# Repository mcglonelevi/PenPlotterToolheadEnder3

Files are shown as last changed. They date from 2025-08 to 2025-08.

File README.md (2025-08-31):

# Pen Plotter for Ender 3 / Ender 3 V2
## Introduction
I had an old Ender 3 V2 that was sitting around collecting dust.  I thought it would be fun to make a pen plotter attachment for the Ender 3 V2.  In case others were interested in making it, I am making this open-source under the MIT license.

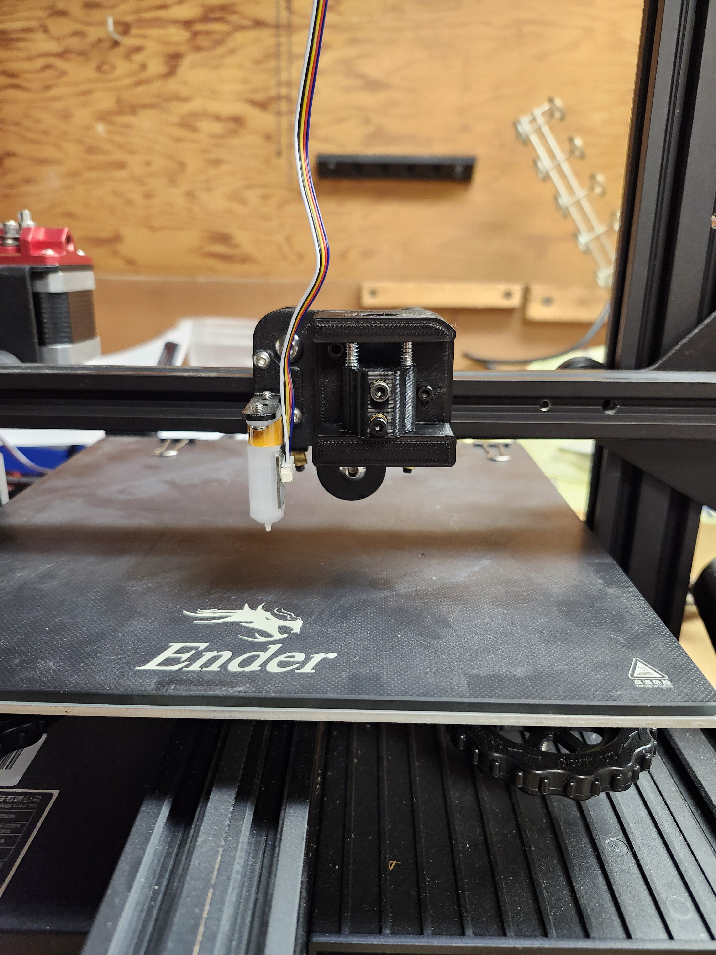
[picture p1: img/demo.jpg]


## Demo
I made a YouTube video showcasing the toolhead in action: https://www.youtube.com/watch?v=6iu8gkPlm34

## Design Constraints
I looked at other pen plotting attachments for the ender 3 V2.  I wanted the following features in my build:
1. I wanted the pen to have some pressure via springs to account for an unlevel bed.
2. I am running [Jyers Marlin firmware](https://github.com/Jyers/Marlin) on my Ender 3 V2 with a BL Touch.  I didn't want to install the old endstops, so I made my solution compatible with models of the Ender 3 with a BL touch.

## Bill of Materials
1. About 25 grams of PLA or equivalent of your preferred filament.
2. 3mm * 40mm steel rods (2).  I bought [these](https://www.amazon.com/Lyrlidr-Stainless-Industry-Working-Hobbies/dp/B0DCBCRB1C) on Amazon and cut them down to size.
3. 2 M3 brass inserts - I used [these](amazon.com/dp/B0CDH36ZMX?ref=ppx_yo2ov_dt_b_fed_asin_title)
4. 4 M3 screws.  I think M3x20mm should work for most cases.
5. 1 M3 nut.
6. 2 springs.  I used 0.3mm x 4mm x 15mm - Something [like these](https://www.amazon.com/PATIKIL-Compression-Stainless-Mechanical-Assortment/dp/B0DKCRH26S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,industrial,87&sr=1-1&th=1) should work.

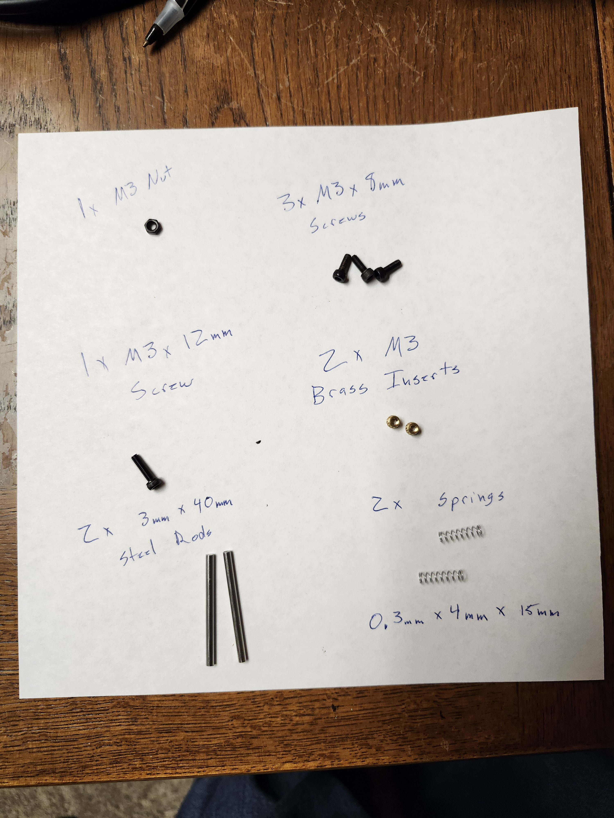
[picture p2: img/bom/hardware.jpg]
Hardware

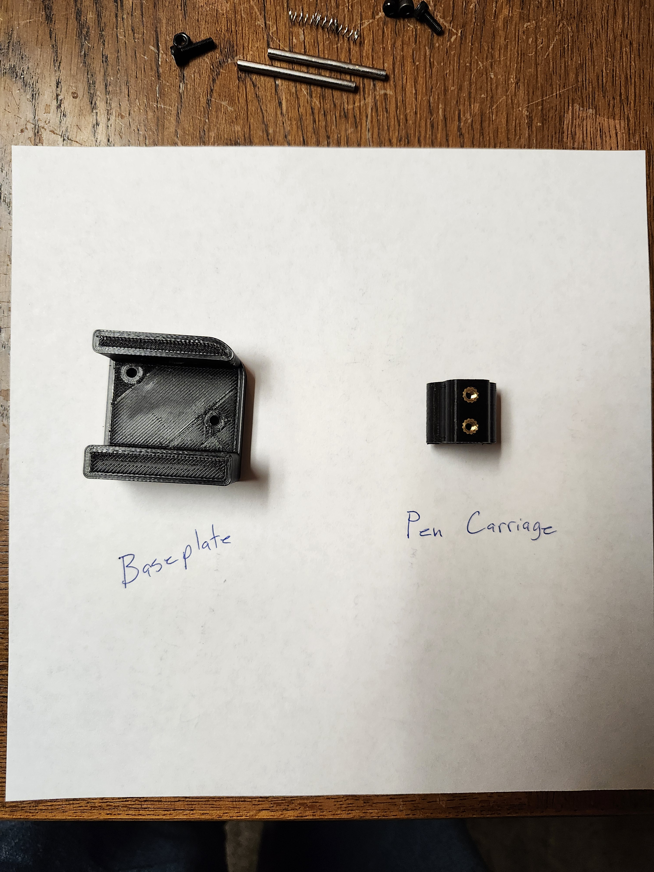
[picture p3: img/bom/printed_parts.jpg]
Printed Parts


## Recommended Print Settings
There are two parts to print in this build - the pen carriage and the base plate that attaches to the printer.  I printed both parts with 4 walls and 40% infill.  No support should be necessary, but there are a few overhangs.  The size of the overhangs are very small though.

## Quick Assembly Instructions
These instructions assume the toolhead and hotend have been removed from your Ender 3.  The instructions for this vary by model, but should involve unscrewing a screw in the back of the toolhead and then 2 screws for the hotend.

### Instructions
1. In the carriage, press 2 brass inserts into the front 2 screw holes.  Use a soldering iron to melt the plastic and press them into place.  For PLA, I would recommend a soldering temp ~525F or 200C [image](https://github.com/mcglonelevi/PenPlotterToolheadEnder3/blob/main/img/assembly/step_1.jpg)
2. Check the fit of the 3mm steel rods in the pen carriage.  The pen carriage should slide but not move.  Depending on the tolerances of your printer, you may need to use a 1/8in drill bit to expand the holes.  Also, some PTFE lube may also help things slide a little easier.
3. Insert the steel rods into the baseplate but do not push them all the way down. [image](https://github.com/mcglonelevi/PenPlotterToolheadEnder3/blob/main/img/assembly/step_3.jpg)
4. Slide the springs over the steel rods. [image](https://github.com/mcglonelevi/PenPlotterToolheadEnder3/blob/main/img/assembly/step_4a.jpg)
5. Compress the spring and move one side of the pen carriage into place and push the steel rod as far in as you can. [image](https://github.com/mcglonelevi/PenPlotterToolheadEnder3/blob/main/img/assembly/step_5a.jpg)  Compress the other spring and insert the other rod through the other hole in the pen carriage. [image](https://github.com/mcglonelevi/PenPlotterToolheadEnder3/blob/main/img/assembly/step_5b.jpg)
6: If the rods are not flush with the top, I would recommend a clamp or a vice or gently hammering the rod into place until its flush with the top.  It should be flush or close to flush with the top of the base plate if the length is close to 40mm. [image](https://github.com/mcglonelevi/PenPlotterToolheadEnder3/blob/main/img/assembly/step_6.jpg)
7. Using 2 M3 x 8MM screws, thread them into the brass inserts on the front of the pen carriage. [image](https://github.com/mcglonelevi/PenPlotterToolheadEnder3/blob/main/img/assembly/step_7.jpg)
8. The base plate has 2 holes for attaching the plate to the printer.  For the right hole, use an M3x8mm screw.  For the right hole, stick a M3x12mm screw through it and the screw should poke through the back of the plate.  Secure it with a nut. [image](https://github.com/mcglonelevi/PenPlotterToolheadEnder3/blob/main/img/assembly/step_8.jpg)

## Calibration
Here are my recommended calibration steps.
1. Using the prepare menu, home all the axes on your printer.  At the end of calibration, it's pretty likely that your Z height will be ~13mm.
2. Using the Move controls on the printer, set the Z axis to ~0.5mm.
3. Insert a pen and let it touch the build plate.  Turn both screws in the pen carriage to secure the pen in place.
4. Lift up on the pen slightly and put a piece of paper in place.  I secure the paper to the build plate with binder clips.
5. Using the controls on the printer, you can manually move the head around for a quick test.  Another option is to disable the stepper motors and move the gantry and bed by hand.  Assuming the lines look nice and solid, your printer is calibrated.

If your pen doesn't make contact with the paper, rerun the calibration steps above but use a slightly higher number on the Z in step 2 (0.7mm or 0.9mm may work better depending on pen and paper thickness).

## Generating G-Code
I followed the instructions from Andrew Sink for the PLTR V2 here:
[https://github.com/AndrewSink/pltr_toolhead](https://github.com/AndrewSink/pltr_toolhead)

Page 18-29 of the user guide shows how to configure Inkscape.

## Debugging GCode
For some reason, my Ender 3 started skipping instructions from the GCode generated from the Inkscape Extension.  It could be that my printer is old and half-dead, so I ended up using [Pronterface](https://www.pronterface.com/) to run the GCode by hooking up my Ender 3 to my laptop via the USB port.  [NC Viewer](https://ncviewer.com/) is also a great tool for verifying the generated GCode.

## Other Recommended Builds / Reads
My design for this was inspired by AndrewSink's PLTR V2 toolhead.  I really recommend looking at the PLTR V2 repo as well.
[PLTR V2](https://github.com/AndrewSink/pltr_toolhead)

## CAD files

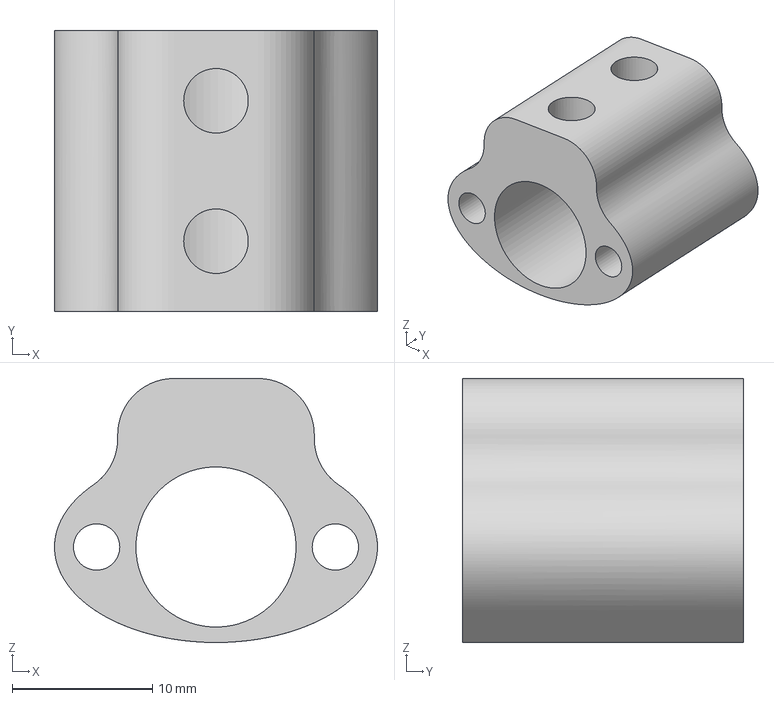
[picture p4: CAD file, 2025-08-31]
parts/pen_carriage.3mf
23.0 x 20.0 x 18.8 mm

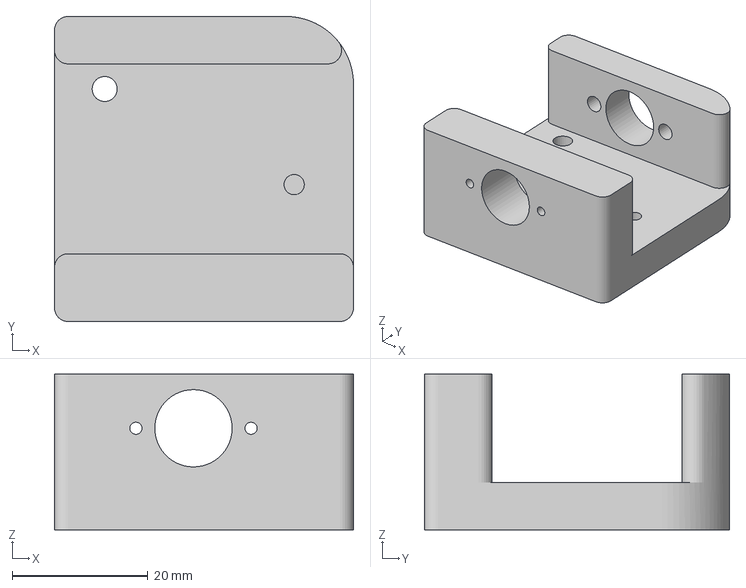
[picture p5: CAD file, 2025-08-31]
parts/baseplate.3mf
44.1 x 45.0 x 23.0 mm

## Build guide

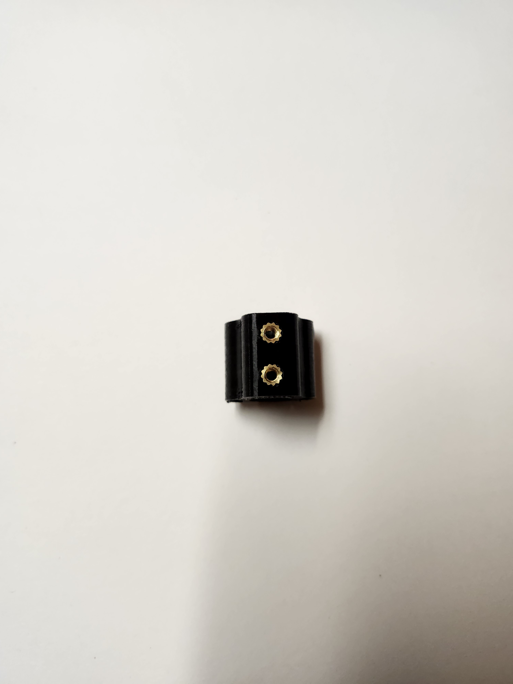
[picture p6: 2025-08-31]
img/assembly/step_1.jpg

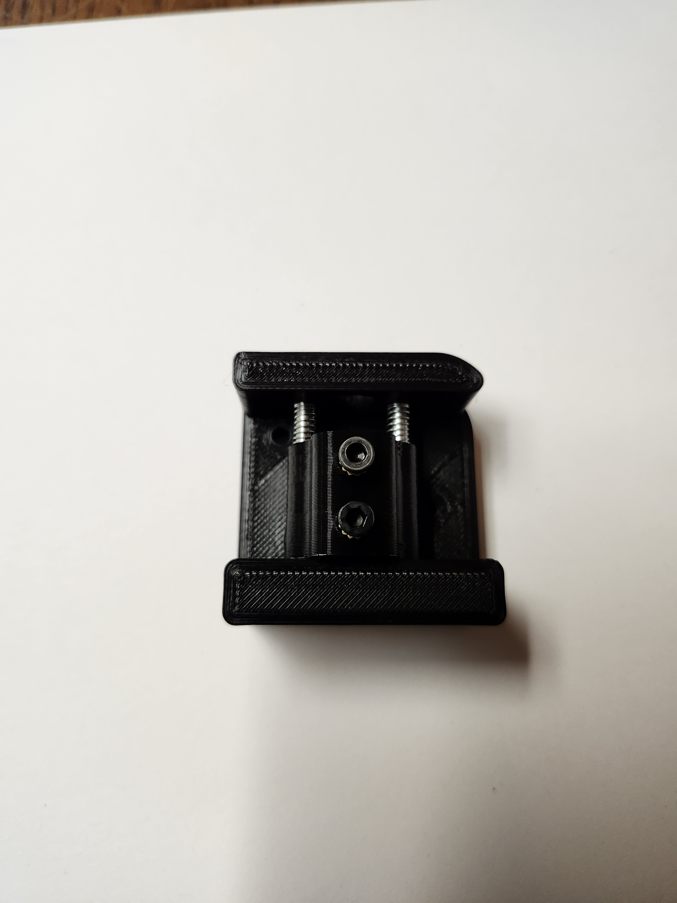
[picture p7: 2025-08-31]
img/assembly/step_7.jpg

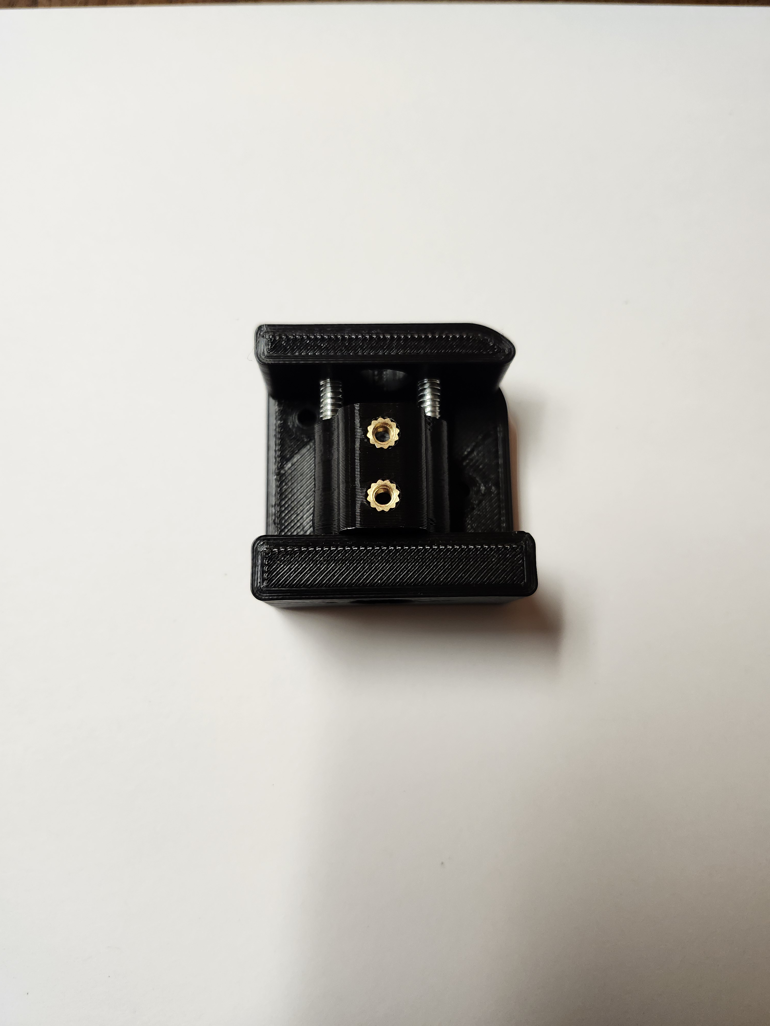
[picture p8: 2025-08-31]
img/assembly/step_6.jpg

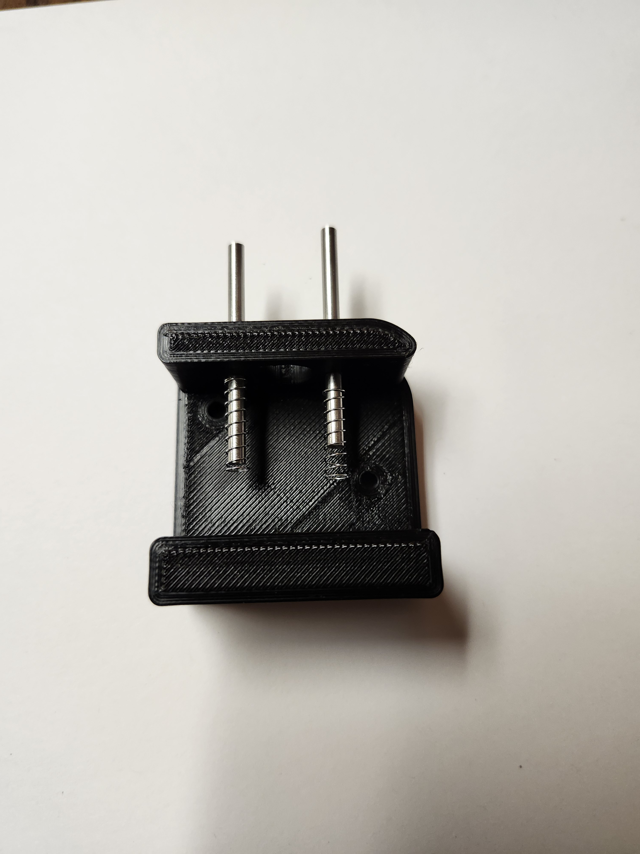
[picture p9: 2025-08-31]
img/assembly/step_4a.jpg

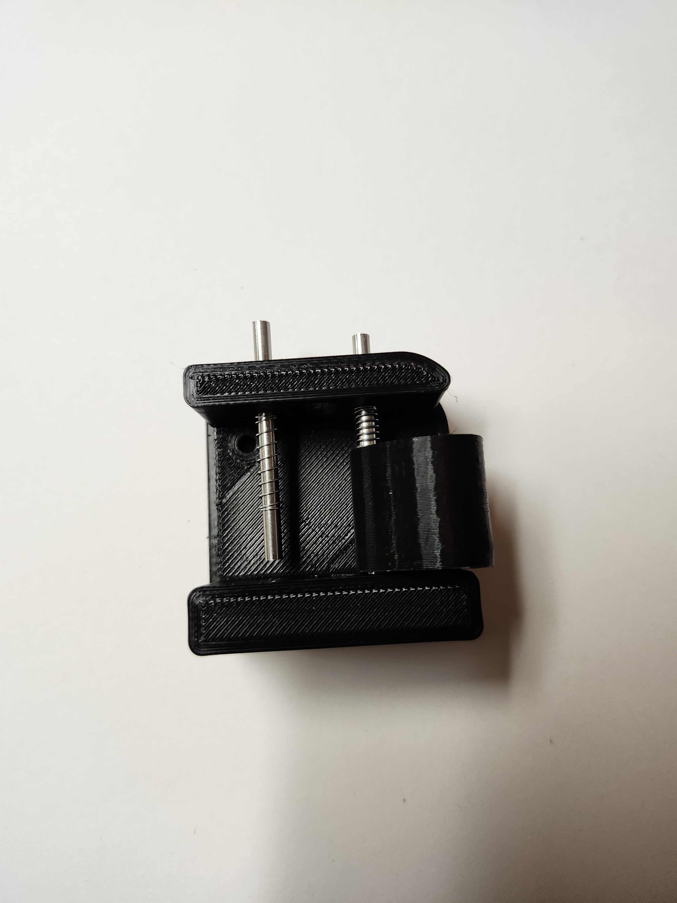
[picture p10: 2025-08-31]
img/assembly/step_5a.jpg

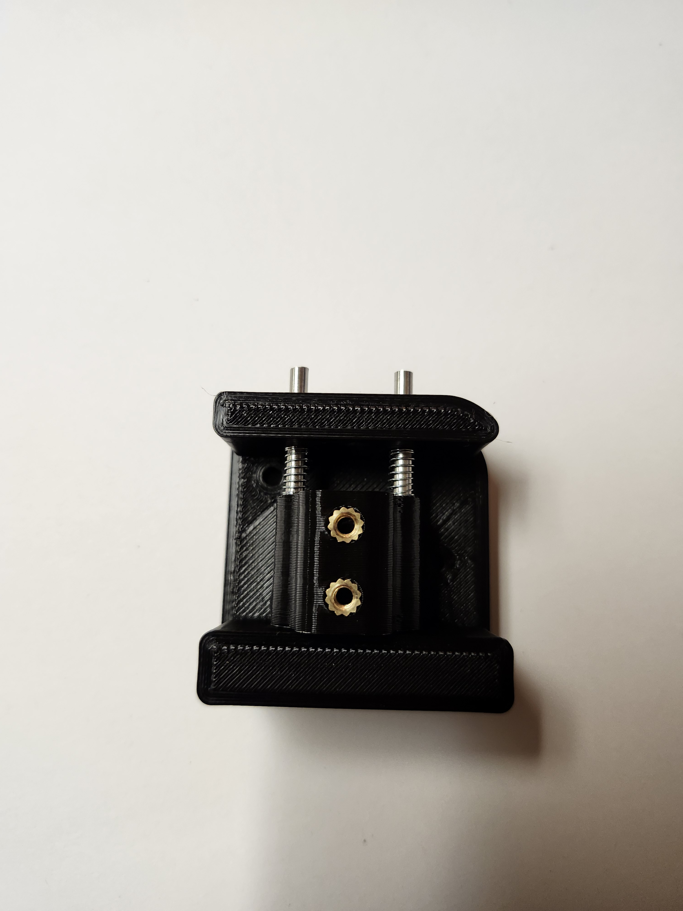
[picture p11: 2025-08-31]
img/assembly/step_5b.jpg
